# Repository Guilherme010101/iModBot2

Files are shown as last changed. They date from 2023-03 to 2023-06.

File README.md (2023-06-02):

# Project Presentation 
This iModBot project consists of a low-cost modular robot that can be programmed using block programming language and/or C/C++ language.
This project has a library to facilitate the control of the robot.

Block programming is divided into 4 levels to facilitate user learning. The levels are as follows:
 - Beginner level -> It is possible to have the robot perform a task with 1 to 2 blocks.
 - Normal level -> The user has more control over the movement of the robot, he only has the loop function.
 - Middle level -> The user can now place blocks in the Setup and Loop function.
 - Advanced level -> The user has all the functions of the library and needs to configure all aspects of the robot.
    
ROBOT

# How to transfer files from GitHub
On GitHub it's not possible to upload any file individually. It's recommended to transfer all folders and files present in this project. To do so, follow the instructions below:

Start by downloading all files in .zip format.


Open the location of the downloaded .zip file and use a program to extract the contents.


Finally you'll get a set of folders and files organized in the same way as they are in this repository.



# Project Elaboration
**1st Step of the Project**

To assemble the robot just follow the document 3-03_iModBot_Offline_Assembly_Guide ([3-03_iModBot_Offline_Assembly_Guide.pdf](https://github.com/Guilherme010101/iModBot2/blob/master/3_Documents/3-03_iModBot_Offline_Assembly_Guide.pdf)) that shows how to assemble or watch the video [iModBot@ipleiria.pt guia de montagem](https://www.youtube.com/watch?v=i4wFh0GqzkM&feature=emb_logo). This document also includes a listing of components that will be needed for its assembly. To better understand what each component of the robot does, you can read the technical manual ([3-01_iModBot_Tech_Manual.pdf](https://github.com/Guilherme010101/iModBot2/blob/master/3_Documents/3-01_iModBot_Tech_Manual.pdf)) which explains various aspects of the robot.

Material list:
 * ESP32 wroom32 devkit ; 
 <p align="center">
  
</p>

 * l293d 4 channel module ;
 <p align="center">
  
</p>   

 * 2x LM393 speed sensor ; 
 <p align="center">
  
</p> 

 * BFD-1000 5CH ;
  <p align="center">
  
</p>   

 * HC-SR04 ;
  <p align="center">
  
</p> 

 * I2C level shifter ; 
 <p align="center">
  
</p> 

 * TP4056 ; 
 <p align="center">
  
</p> 

 * li-ion rechargable battery 2500 mAh ; 
 <p align="center">
  
</p> 

 * Jumper wire male male, Jumper wire male female ; 
 <p align="center">
  
</p> 

 * 2wd smart robot kit . 
 <p align="center">
  
</p> 

**2nd Step of the Project** 
 
 Downloads:
 
- Library iModBot.rar ([4_Files/4-3_Libraries/iModBot.rar](https://github.com/Guilherme010101/iModBot2/blob/master/4_Files/4-3_Libraries/iModBot.rar)) and unzip the file. Anotação 2020-06-25 170046

- Arduino IDE software on [pagina do Arduino](https://www.arduino.cc/en/main/software), install the version that suits your equipment, for windows we recommend the option "windows installer, for windows 7 and up". 
 - Bear in mind that the project contents were developed and tested in the Arduino IDE 1.8.12 version, they should continue to be compatible with the most recent versions of this software.
       <p align="center">
  
</p> 

- ArduBlock java file ([4_Files/4-4_ArduBlock/ArduBlock_20220615.jar](https://github.com/Guilherme010101/iModBot2/blob/master/4_Files/4-4_ArduBlock/ArduBlock_20220615.jar)).

Anotação 2020-06-25 172512

**3rd Step of the Project**

Read and follow the tutorials to configure the Arduino:
 - Configure Arduino IDE for ESP32; ([3_Documents/3-04_Add_ESP32_Arduino_IDE.pdf](https://github.com/Guilherme010101/iModBot2/blob/master/3_Documents/3-04_Add_ESP32_Arduino_IDE.pdf)).

 - Configure ArduBlock in Arduino IDE; ([3_Documents/3-05_Add_ArduBlock_Arduino_IDE.pdf](https://github.com/Guilherme010101/iModBot2/blob/master/3_Documents/3-05_Add_ArduBlock_Arduino_IDE.pdf)).

 - How to install libraries in Arduino IDE. ([3_Documents/3-06_Add_Arduino_IDE_Libraries.pdf](https://github.com/Guilherme010101/iModBot2/blob/master/3_Documents/3-06_Add_Arduino_IDE_Libraries.pdf)).

# Documentation

After having the Arduino IDE and ArduBlock installed, you can take advantage of the available tutorials. These tutorials teach how to work with the robot and are divided into two categories: tutorials for ArduBlock and tutorials for Arduino IDE.

**ArduBlock documentation**

The [4 levels](https://github.com/Guilherme010101/iModBot2/tree/master/1_Tutorials/1-1_ArduBlock_Tutorials) below will facilitate and guide how to use each block and how to create a program.

- [Beginner level;](https://github.com/Guilherme010101/iModBot2/tree/master/1_Tutorials/1-1_ArduBlock_Tutorials/Tutorial_1_-_Begginer%20Level)

- [Normal level;](https://github.com/Guilherme010101/iModBot2/tree/master/1_Tutorials/1-1_ArduBlock_Tutorials/Tutorial_2_-_Normal_Level)

- [Middle level;](https://github.com/Guilherme010101/iModBot2/tree/master/1_Tutorials/1-1_ArduBlock_Tutorials/Tutorial_3_-_Intermediate_Level)

- [Advanced level.](https://github.com/Guilherme010101/iModBot2/tree/master/1_Tutorials/1-1_ArduBlock_Tutorials/Tutorial_4_-_Advanced_Level)

There is a set of activities for each level. After reading the documentation of a level, you will be able to carry out the corresponding activity in [2_Activities/2-1_ArduBlock_Activities/](https://github.com/Guilherme010101/iModBot2/tree/master/2_Activities/2-1_ArduBlock_Activities).

**Arduino IDE documentation**

After having done the ArduBock tutorials, you should have a better idea of how to program in the Arduino IDE. We've also designed some tutorials and activities to make learning easier.

- [Tutorial 1 - Movement;](https://github.com/Guilherme010101/iModBot2/tree/master/1_Tutorials/1-2_Arduino_IDE_Tutorials/Tutorial_1_-_Movement)

- [Tutorial 2 - Sensors;](https://github.com/Guilherme010101/iModBot2/tree/master/1_Tutorials/1-2_Arduino_IDE_Tutorials/Tutorial_2_-_Sensors)

- [Tutorial 3 - Follow path.](https://github.com/Guilherme010101/iModBot2/tree/master/1_Tutorials/1-2_Arduino_IDE_Tutorials/Tutorial_3_-_Follow_Path)

The activities for each tutorial are available at [2_Activities/2-2_Arduino_IDE_Activities/
](https://github.com/Guilherme010101/iModBot2/tree/master/2_Activities/2-2_Arduino_IDE_Activities).

# Edit the ArduBlock

If you are interested in creating a block, you should follow the steps in this folder [4_Files/4-4_ArduBlock/](https://github.com/Guilherme010101/iModBot2/tree/master/4_Files/4-4_ArduBlock).

# Augmented Reality

Using the Unity3d game engine, ROS2 and our robot library, create your virtual world, project it into the real world and watch the robot interact with it.
This functionality is still under development and for now it is still very limited.

# Remote controllers

With the controllers for the popular consoles PS3 and PS4, you can control the robot remotely via bluetooth. The library is easy to install and only needs one program, the Arduino IDE. Simply input desired values into the code, such as steering sensitivity, motors acceleration, maximum speed, and much more!

# Authors
 
- Abel Teixeira   - student at [Polytechnic of Leiria](https://www.ipleiria.pt/cursos/) of the TeSP course in Electronics and Telecommunications Networks, GitHub: [Ab-Tx](https://github.com/Ab-Tx)
- Samuel Lourenço - student at [Polytechnic of Leiria](https://www.ipleiria.pt/cursos/) of the TeSP course in Automation, Robotics and Industrial Maintenance, GitHub: [SamueLourenc0](https://github.com/SamueLourenc0)
- Nelson Henriques - student at [Polytechnic of Leiria](https://www.ipleiria.pt/cursos/) of the TeSP course in Automation, Robotics and Industrial Maintenance, GitHub: [NetchoExtreme](https://github.com/NetchoExtreme)
- Paulo Sousa - student at [Polytechnic of Leiria](https://www.ipleiria.pt/cursos/) of the TeSP course in Electronics and Telecommunications Networks, GitHub [DimitriOnLSD](https://github.com/DimitriOnLSD)
- Guilherme Dias - student at [Polytechnic of Leiria](https://www.ipleiria.pt/cursos/) of the TeSP course in Automation, Robotics and Industrial Maintenance, GitHub [Guilherme010101](https://github.com/Guilherme010101)

## Guided by:
- Luís Conde - [Polytechnic of Leiria](https://www.ipleiria.pt), GitHub: [Luís Conde](https://github.com/conde-ISR-UC-PT)
- Carlos Neves - [Polytechnic of Leiria](https://www.ipleiria.pt), [INESC-Coimbra](http://inescc.estg.ipleiria.pt/), GitHub: [Carlos Neves](https://github.com/carlos-neves)

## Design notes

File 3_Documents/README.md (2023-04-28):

# Documents

Inside this folder you will find documentation for the various project aspects and their respective DOCX files for editing:

- `src`
  - Word source files.

- **3-00_iModBot_Components_List.xlsx**
  - Supplies the list components used in iModBot, with some of their respective buy stores and prices.

- **3-01_iModBot_Tech_Manual.pdf**
  - Describes the components used in the project, the functions provided by the library and other aspects.

- **3-02_iModBot_Assembly_And_Software_Installation_Tutorial.pdf**
  - Teaches you how to install the necessary tools and how to assemble the robot.

- **3-03_iModBot_Offline_Assembly_Guide.pdf**
  - Provides a list of components and shows the connections that must be made between the components.

- **3-04_Add_ESP32_Arduino_IDE.pdf**
  - Explains how to connect the ESP32 development board to the Arduino IDE software.

- **3-05_Add_ArduBlock_Arduino_IDE.pdf**
  - Explains how to install ArduBlock in the Arduino IDE software.
  
- **3-06_Add_Arduino_IDE_Libraries.pdf**
  - Explains how to install libraries in the Arduino IDE software.
  
- **3-07_Edit_ArduBlock_Files.pdf**
  - It teaches how to install all the tools needed to edit the ArduBlock Workspace.

- **3-08_Create_ArduBlock_Blocks.pdf**
  - Teaches how to create a block in ArduBlock using the Eclipse IDE.

- **3-09_Add_Eclipse_IDE_Libraries.pdf**
  - Explains how to add libraries to the Eclipse IDE software.

- **3-10_Update_JDK.pdf**
  - Guide to update the Java version for using the Eclipse IDE.

- **3-11_Openblock_Error_Tutorial.pdf**
  - Troubleshooting guide for error in openblocks install.

- **3-12_Basic_Eletronics_Assembly_Guide.pdf**
  - A basic assembly guide is provided to acquaint you with the Breadboard and how it works when mounting electronic boards in this tool.

- **3-13_Remote_Bluetooth_Dualshock.pdf**
  - A tutorial is provided on how to set up the code to pair a dualshock 3 or 4 controller to control the robot remotely via Bluetooth.

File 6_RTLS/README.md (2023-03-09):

# RTLS

Folder tree:
```
6_RTLS
├── DRTLS_Manager_source_R2.0/
├── DWM1001_DWM1001-DEV_MDEK1001_Sources_and_Docs_v9/
├── Scripts/
└── esp32-dwm1001_Workspace/

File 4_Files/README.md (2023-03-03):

# Files

Folder tree:
```
4_Files
├── 4-1_PCB_Files/        // 2 PCB versions
├── 4-2_3D_Files/         // Cases for the batteries and side motor supports
├── 4-3_Libraries/        // Dualshock libraries for remote controllers and iModBot library for various other functions
└── 4-4_ArduBlock/        // ArduBlock file for Arduino IDE and ArduBlock-Workspace for editing or creating blocks
```
## Software

To be able to edit source files inside the folders, you will need the following programs:

`Eclipse IDE` This is used to edit the ArduBlock-Workspace file. In there, you can edit or create blocks, change default values or create new ones, change blocks image, etc. Tutorials for installing this program, along with JDK and maven, can be found in the 3-Documents folder.

`EAGLE` This is used to open and edit the first PCB version. 

`Proteus 8.10` This is used to open and edit the second PCB version. Keep in mind that this file can't be opened in previous versions of proteus, like 8.9.

`Fusion 360` `SolidWorks` `SketchUp Pro 2021` These can be used to open and edit the .F3D, .step and .skp files inside Battery_Case_3D folder.

`Visual Studio Code` This is used to edit the .h and .cpp files inside both libraries.

`Arduino IDE` This is used to upload the code to the ESP32.

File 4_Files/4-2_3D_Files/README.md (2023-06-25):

# 3D Battery cases

__Prototype 1__

`bat case v9.step`
Features the most recent version for single battery case for this prototype.

__Prototype 2__

`Battery_Holder.skp`
Features the most recent version for single battery case for this prototype.

`Battery_Holder_Stacked.skp`
Features an inside battery stacking with no middle layer. Simple use and faster printing but not recommended.

`Battery_Holder_Slot.skp`
Features an inside battery stacking with removable middle layer.

`Battery_Holder_Under_Robot`
Features the most recent version of the double batterry case that's under the iModBot chassis.

`Infrared_Sensor_Piece.stl`
3D printable piece to allow the sensor to work properly.

`Infrared_Sensor_Piece_Thicker_Filament.stl`
3D printable piece to allow the sensor to work properly. Should be used if the filament used to print the piece is thicker than normal.

__Others__

`motors_side_support_v3.stl`
3D printable piece for side supports in iModBot chassis.

## Information

This folder contains all cases used in iModBot for the batteries and the ifrared sensor. All outter holes dimensions are specifically designed for the iModBot chassis alone. 

Sterolithography files (STL) can be opened directly with CURA software for 3D printing. 

SketchUp (SKP), Fusion 360 (F3D), Standard for the Exchange of Product Data (STEP) and Autodesk Inventor Part files are the given open-source files. SkethUp files were saved with 2021 version.

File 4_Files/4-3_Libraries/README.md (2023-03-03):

# Dualshock and iModBot Libraries

These libraries were written in C/C++ programming language. You will find instructions on how to install these and upload them to the ESP32 inside the  [3-Documents](https://github.com/Guilherme010101/iModBot2/tree/master/3_Documents) folder. Inside you can also find information regarding the robots' various functions.

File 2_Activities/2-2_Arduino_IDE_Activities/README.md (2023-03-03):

# Atividades para Arduino IDE

As presentes atividades podem ser realizadas com recurso ao software Arduino IDE utilizando a linguagem de programação C/C++.

Ps tutoriais associados estão presentes em [/1_Tutoriais/1-2_Tutoriais_para_Arduino_IDE/](https://github.com/Guilherme010101/iModBot2/tree/master/1_Tutorials/1-2_Arduino_IDE_Tutorials).

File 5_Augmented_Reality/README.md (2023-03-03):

# Augmented Reality

Using the Unity3d game engine, ROS2 and our robot library, create your virtual world, project it into the real world and watch the robot interact with it.

This functionality is still under development and for now it is still very limited.

## Requirements

 - Ubuntu 20.04 (Native ou Virtual)
 - Consult the document [Tutorial_SetUp_VM](https://github.com/Guilherme010101/iModBot2/blob/master/5_Augmented_Reality/Tutorial_SetUp_VM.pdf) to install it on a Virtual Machine (native installation is recommended).
 
 - Docker  
 - Consult the document [Tutorial_docker](https://github.com/Guilherme010101/iModBot2/blob/master/5_Augmented_Reality/Tutorial_docker.pdf) to install it and understand how it works.

## Utilization

1. Open a terminal in the folder [iModBot-Docker](https://github.com/Guilherme010101/iModBot2/tree/master/5_Augmented_Reality/iModBot-Docker).
   
2. Create the Docker image (this step takes some time).
    ```bash
    $ ./build-docker-image.bash
    ```
3. Starts the created image.
    ```bash
    $ ./run-docker-container
    ```
4.  Open the `VScode`.
    ```bash
    $ code
    ```
	  -  Install the PlatformIO extension and open the folder [VScode_Workspace\ESP32-ROS2_iModBot](https://github.com/Guilherme010101/iModBot2/tree/master/5_Augmented_Reality/iModBot-Docker/VScode_Workspace/ESP32-ROS2_iModBot), put the id and password of your Wifi network and the IP of the container.
	  - Uploads the program to the ESP32.
	  - Save changes and close VScode.
    
5. Start the `Unity Hub` and install the latest editor and open the project found in the folder [iModBot-Docker\Unity_Workspace](https://github.com/Guilherme010101/iModBot2/tree/master/5_Augmented_Reality/iModBot-Docker/Unity_Workspace/iModBot-UnityRos2).
    ```bash
    $ cd unity && ./UnityHub.AppImage
    ```
6.  Start the ROS2 Node.
 - In the terminal of the native machine that is in the folder iModBot-Docker opens a new terminal in the container.
    ```bash
    $ ./new_bash_in_container
    ```
 - In the new terminal:
    ```bash
    $ cd work/ROS2_Workspace && . install/setup.bash && ros2 run stop_oncollision oncollision
    ```
7. Starts the remote control (it can be accessed in any browser as long as it is on the local network, through the IP that appears in the window).
- Open 2 new terminals in the container, as described earlier.
- On the 1st:
    ```bash
    $ cd ros2-web-bridge && export DEBUG=ros2-web-bridge:* && node bin/rosbridge.js
    ```
- On the 2nd:
    ```bash
    $ cd ros2-web-bridge/demo && http-server -c-1
    ```
 
8. Start the MicroXRCEAgent (responsible for establishing communication between ROS2 and ESP32).
- Opens a new terminal in the container.
- Starts the program.
    ```bash
    $ MicroXRCEAgent udp4 -p 2018
    ```
Everything is ready to start your journey with augmented reality.
Whenever you want to reopen the container, run the script [start-docker-container](https://github.com/Guilherme010101/iModBot2/blob/master/5_Augmented_Reality/iModBot-Docker/start-docker-container.bash).

Demo video: [https://youtu.be/DlAx3p5d99E](https://youtu.be/DlAx3p5d99E)

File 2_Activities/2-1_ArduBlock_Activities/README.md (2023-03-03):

# Atividades para ArduBlock

Os presentes tutoriais deverão facilitar a compreensão da linguagem de programaçãopor blocos bem como o seu uso no presente projeto.

Pode encontrar os tutoriais associados em [/1_Tutoriais/1-1_Tuturiais_para_ArduBlock/](https://github.com/Guilherme010101/iModBot2/tree/master/1_Tutorials/1-1_ArduBlock_Tutorials).

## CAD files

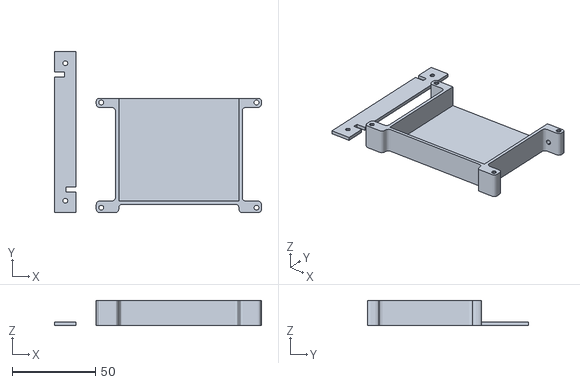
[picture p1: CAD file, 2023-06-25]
4_Files/4-2_3D_Files/Battery_Holden_Under_Robot.stl
124.0 x 96.7 x 15.0

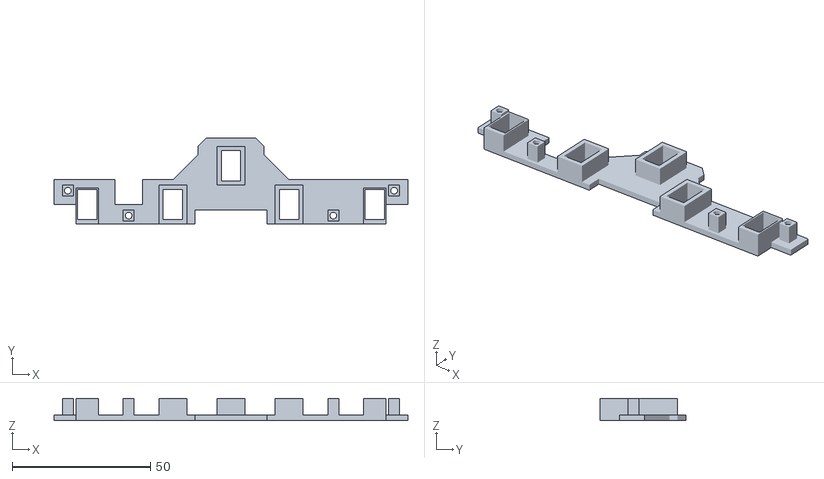
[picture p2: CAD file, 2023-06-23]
4_Files/4-2_3D_Files/Infrared_Sensor_Piece_Thicker_Filament.stl
128.0 x 31.0 x 8.00

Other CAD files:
4_Files/4-2_3D_Files/Infrared_Sensor_Piece.stl
4_Files/4-2_3D_Files/Batterry_Holder_Under_Robot.ipt
4_Files/4-2_3D_Files/Infrared_Sensor_Piece.ipt
4_Files/4-2_3D_Files/Infrared_Sensor_Piece_Thicker_Filament.ipt

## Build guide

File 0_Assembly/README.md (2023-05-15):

# Assembly

PDF files on the main folder and DOCX files on the src folder with instructions on how to assemble the robot and install the necessary tools, and how to upload sketches to ESP32 OTA (Over The Air), with an arduino file on the main folder.

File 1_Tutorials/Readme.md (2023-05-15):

# Tutorials

Tutorials for ArduBlock contain educational content for block programming.

The tutorials for Arduino IDE contain educational content for C/C++ programming.

Activities are provided for each tutorial, they can be found in [2_Activities](https://github.com/Guilherme010101/iModBot2/tree/master/2_Activities).

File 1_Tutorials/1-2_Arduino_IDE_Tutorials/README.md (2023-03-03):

# Tutoriais para Arduino IDE

Os presentes tutoriais deverão facilitar a compreensão da linguagem de programação C/C++ bem como o seu uso no presente projeto.

Pode encontrar as atividades associadas em [/2_Atividades/2-2_Atividades_para_Arduino_IDE/](https://github.com/Guilherme010101/iModBot2/tree/master/2_Activities/2-2_Arduino_IDE_Activities).

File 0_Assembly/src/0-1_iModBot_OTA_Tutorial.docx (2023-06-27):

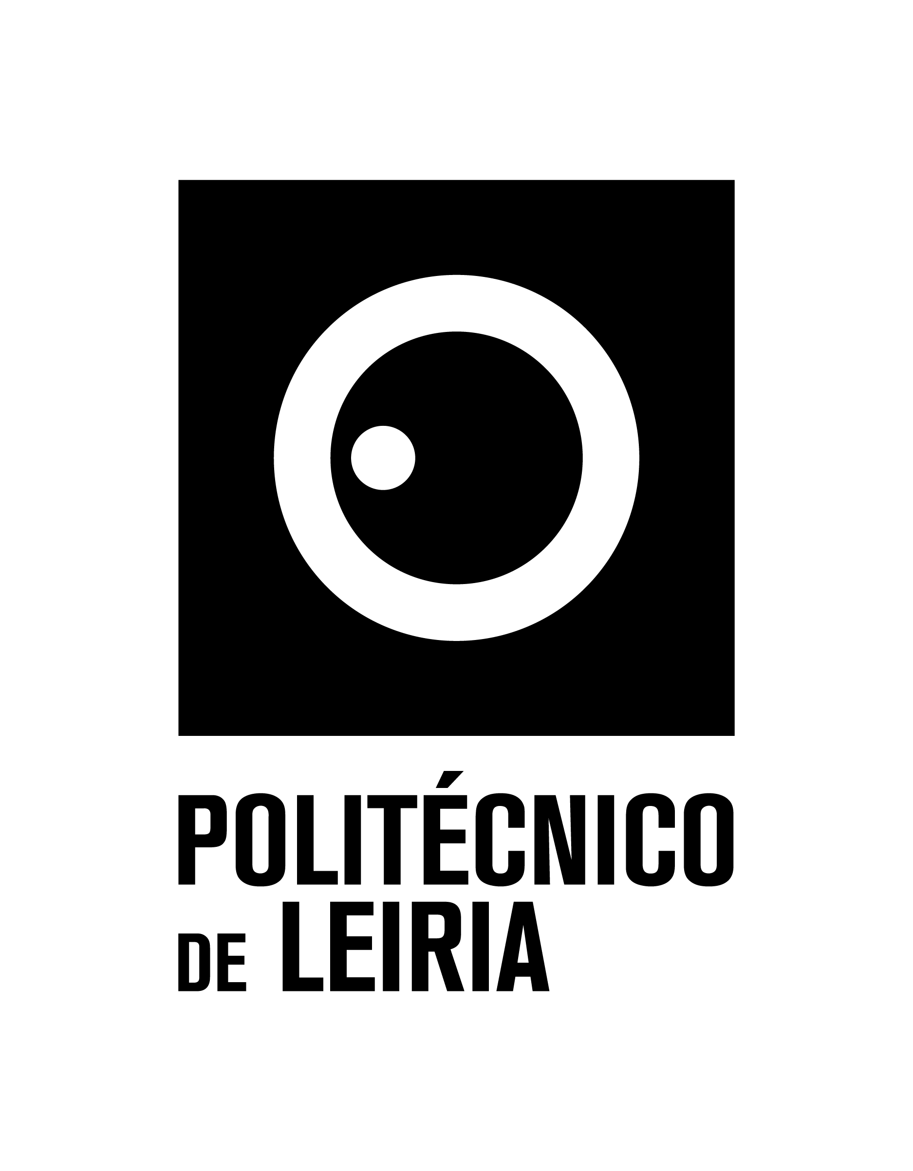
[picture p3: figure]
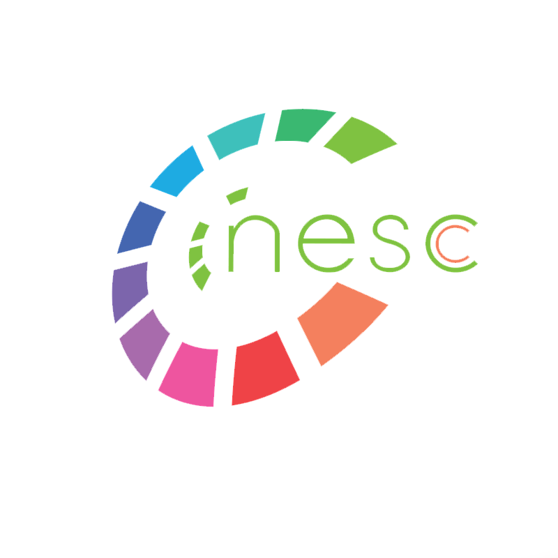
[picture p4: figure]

| Guia de montagem iModBot@ipleiria.pt

# Tutorial de como carregar programas para o ESP32 via WiFi

O robô iModBot é um veículo elétrico de pequenas proporções controlado pelo microcontrolador ESP32. Este microcontrolador pode ser programado usando a linguagem C/C++ e o software gratuito Arduino IDE.

Este tutorial vai focar-se na funcionalidade OTA (Over the Air), que permite carregar programas para o ESP32 usando uma conexão WiFi em vez de se utilizar um cabo entre o computador e o microcontrolador. Este tipo de funcionalidade é essencial para este projeto porque a estrutura do iModBot não permite uma conexão física entre o computador e o ESP32, visto que a sua entrada USB está bloqueada pela caixa das baterias, e assim não é necessário estar a tirar e pôr o ESP32 na placa sempre que seja preciso inserir um novo programa.

1º Passo: Conecte o ESP32 ao seu computador através de um cabo micro-usb.

2º Passo: Vá a “Ferramentas” e selecione o modelo da placa ESP32 e a respetiva porta COM.

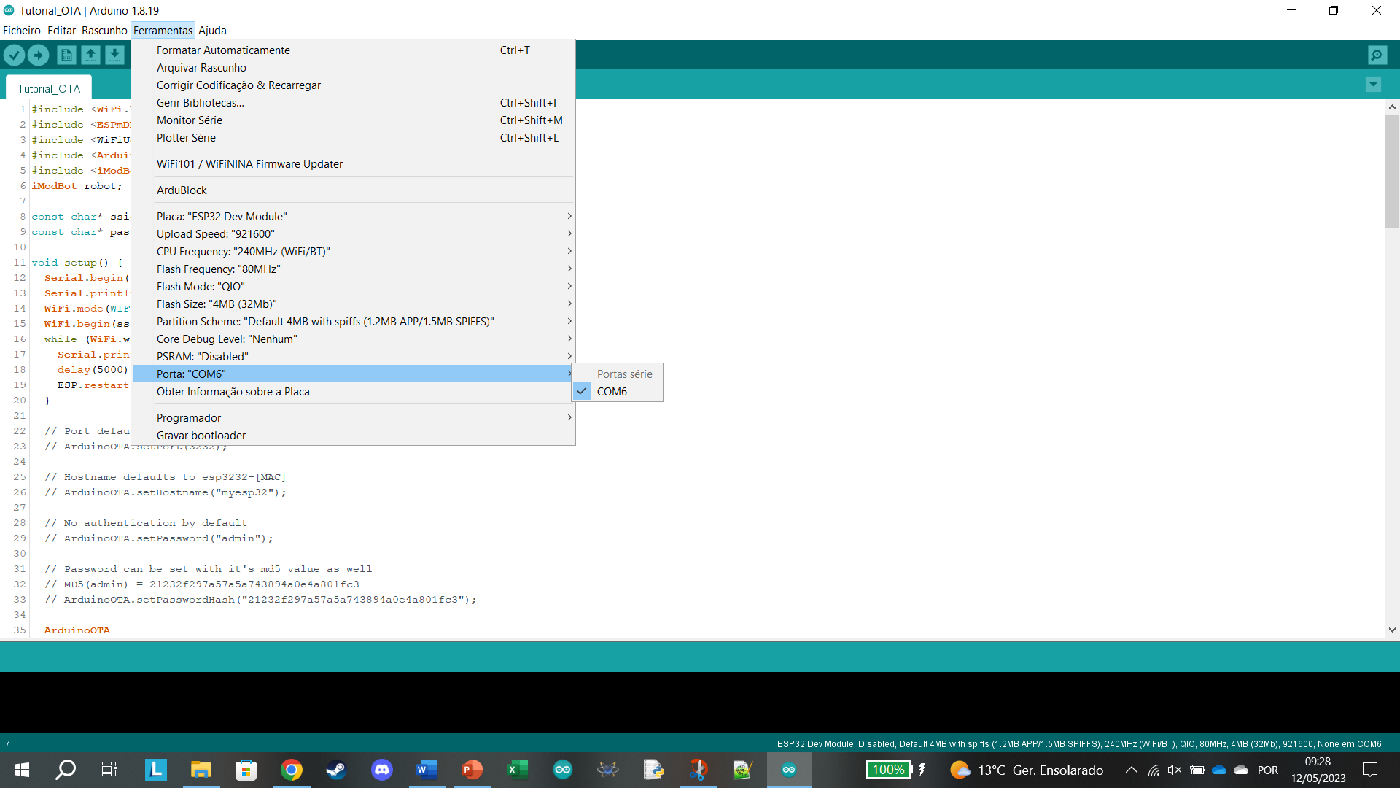
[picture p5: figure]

3º Passo: Copie o seguinte código para o Arduino IDE e nele mude o “ssid” e a “password” pelo nome da rede e a sua palavra-passe, respetivamente:

#include <WiFi.h>

#include <ESPmDNS.h>

#include <WiFiUdp.h>

#include <ArduinoOTA.h>

// Replace with your network credentials

const char* ssid = "YOUR_SSID";

const char* password = "YOUR_PASSWORD";

void setup() {

Serial.begin(115200);

Serial.println("Booting");

WiFi.mode(WIFI_STA);

WiFi.begin(ssid, password);

while (WiFi.waitForConnectResult() != WL_CONNECTED) {

Serial.println("Connection Failed! Rebooting...");

delay(5000);

ESP.restart();

}

// Port defaults to 3232

// ArduinoOTA.setPort(3232);

// Hostname defaults to esp3232-[MAC]

// ArduinoOTA.setHostname("myesp32");

// No authentication by default

// ArduinoOTA.setPassword("admin");

// Password can be set with it's md5 value as well

// MD5(admin) = 21232f297a57a5a743894a0e4a801fc3

// ArduinoOTA.setPasswordHash("21232f297a57a5a743894a0e4a801fc3");

ArduinoOTA

.onStart([]() {

String type;

if (ArduinoOTA.getCommand() == U_FLASH)

type = "sketch";

else // U_SPIFFS

type = "filesystem";

// NOTE: if updating SPIFFS this would be the place to unmount SPIFFS using SPIFFS.end()

Serial.println("Start updating " + type);

})

.onEnd([]() {

Serial.println("\nEnd");

})

.onProgress([](unsigned int progress, unsigned int total) {

Serial.printf("Progress: %u%%\r", (progress / (total / 100)));

})

.onError([](ota_error_t error) {

Serial.printf("Error[%u]: ", error);

if (error == OTA_AUTH_ERROR) Serial.println("Auth Failed");

else if (error == OTA_BEGIN_ERROR) Serial.println("Begin Failed");

else if (error == OTA_CONNECT_ERROR) Serial.println("Connect Failed");

else if (error == OTA_RECEIVE_ERROR) Serial.println("Receive Failed");

else if (error == OTA_END_ERROR) Serial.println("End Failed");

});

ArduinoOTA.begin();

Serial.println("Ready");

Serial.print("IP address: ");

Serial.println(WiFi.localIP());

}

void loop() {

ArduinoOTA.handle();

}

4º Passo: Pressione em “Envio”, que é o botão com uma seta a apontar para a direira no canto superior esquerdo, e ao mesmo tempo que está a enviar o programa pressione o botão “Boot” do ESP32 para que ele permitir carregar o programa.

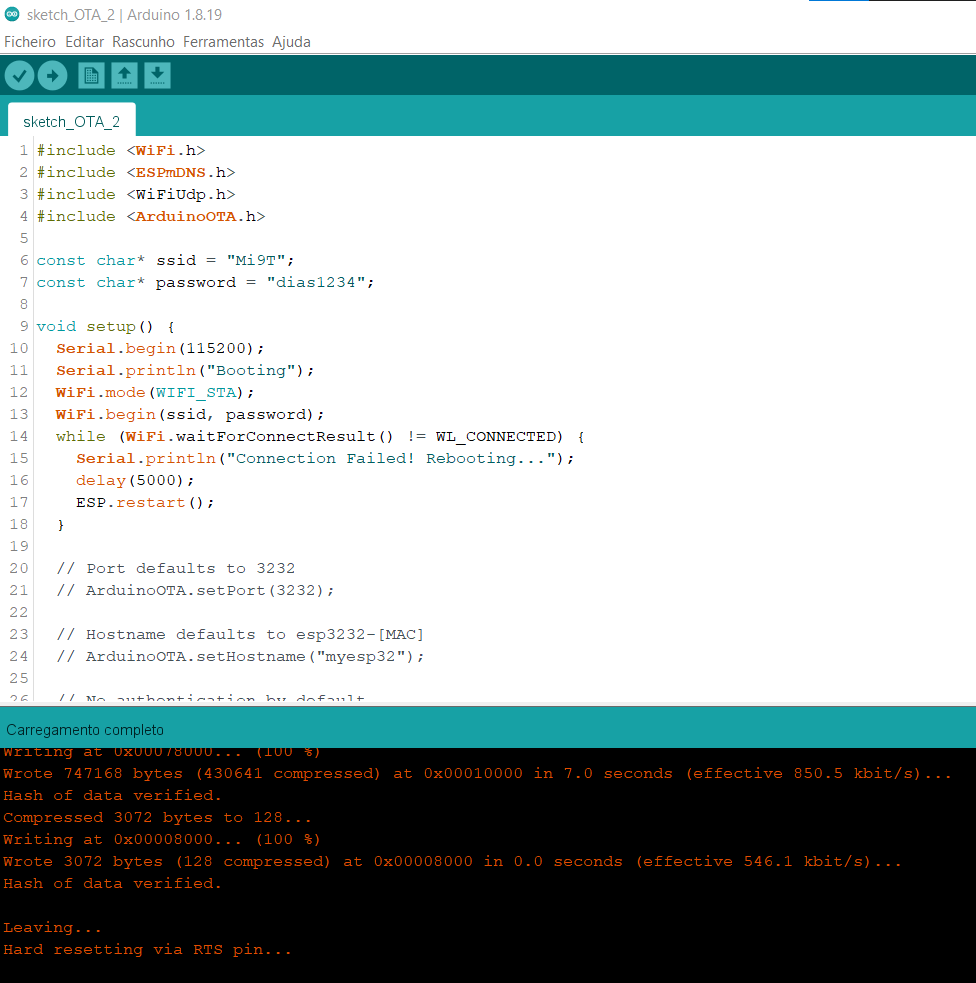
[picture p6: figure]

5º Passo: Abra o “Monitor série” do Arduino IDE, que é o botão com uma lupa no canto superior direito, pressione o botão “EN” do ESP32 para fazer reset e se inseriu as credenciais certa da rede deverá aparecer o endereço IP do ESP.

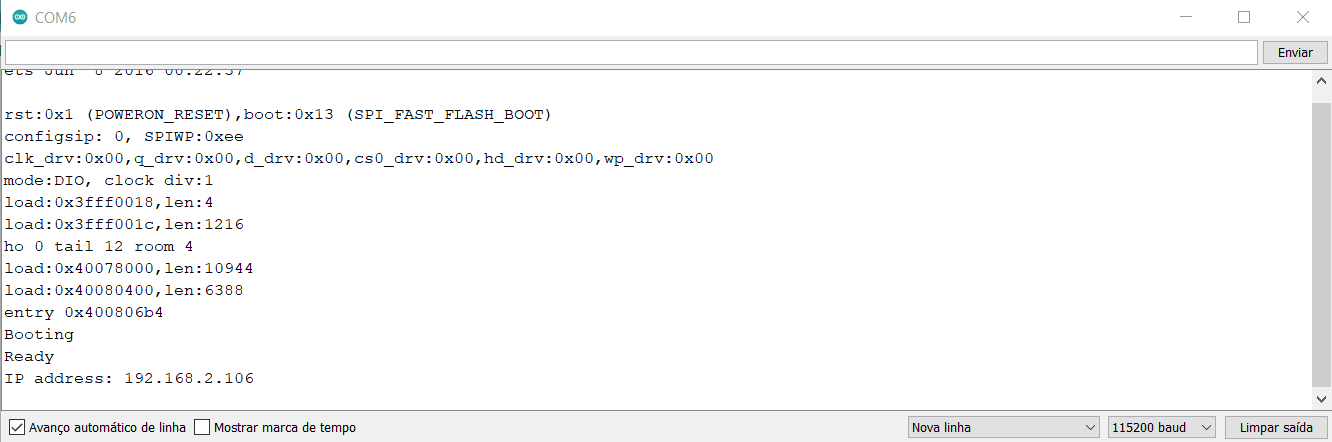
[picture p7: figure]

6º Passo: Agora que o ESP32 está preparado para receber programas OTA, desconecte o microcontrolador do computador, insira-o na placa do iModBot e ligue o robô.

7º Passo: Abra o Arduino IDE, selecione “Ferramentas” e selecione a Porta de rede do ESP32, que deverá ter um aspeto semelhante ao da imagem abaixo:

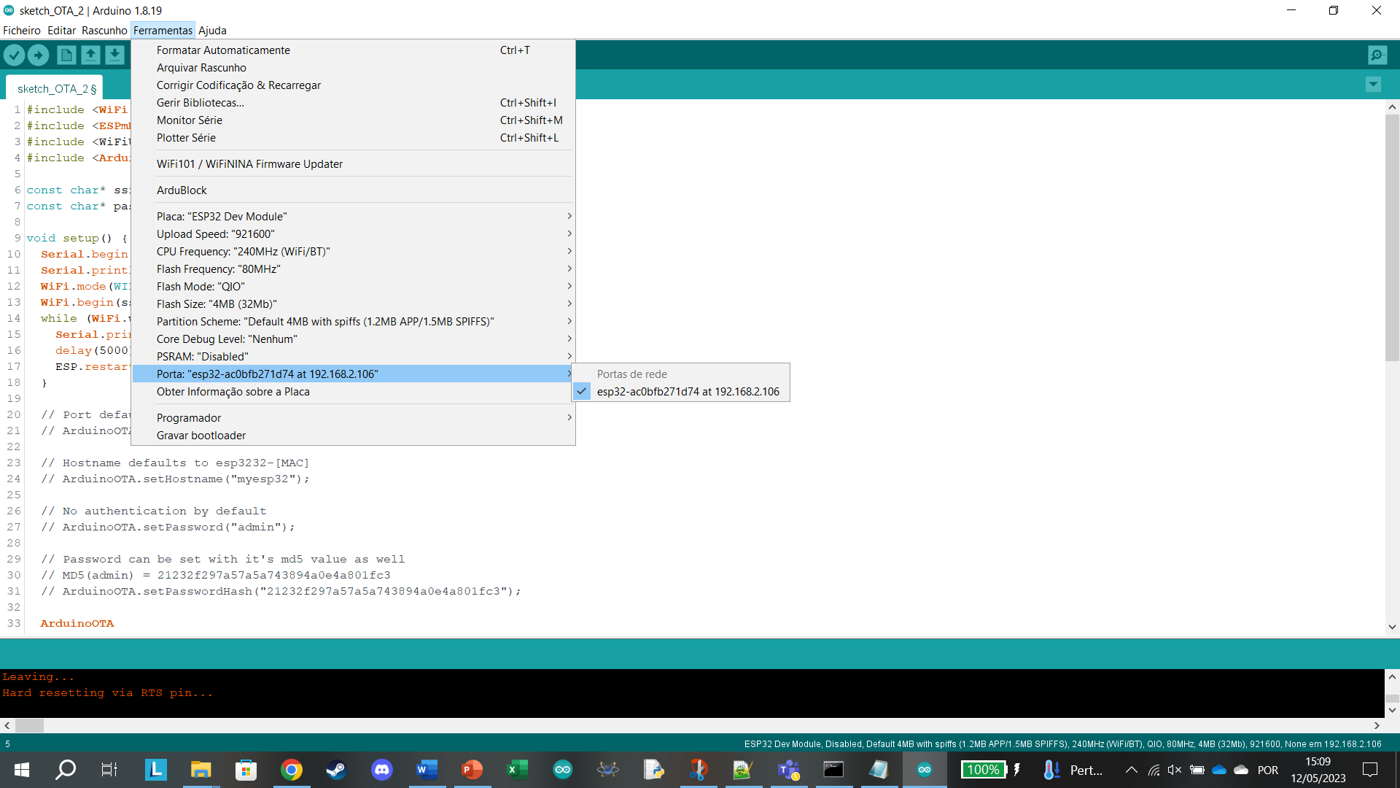
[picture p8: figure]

8º Passo: Com o ESP32 conectado via WiFi basta inserir o código. Para que o código seja compatível com o OTA é necessário inserir o código em si no código básico do OTA. Em baixo está o código do tutorial de controlo de movimentos simples do iModBot sem e com as propriedades do OTA, respetivamente.

### Exemplo controlo de movimentos simples

#include <iModBot.h>

iModBot robot;

void setup()

{

robot.begin();

}

void loop()

{

// Velocidade

// Pode variar de 1 a 255

byte speed = 255;

// Para seguir em frente

robot.forward(speed);

delay(500);

// Para recuar

robot.reverse(speed);

delay(500);

// Rodar para a direita

robot.rotateRight(speed);

delay(500);

// Rodar para a esquerda

robot.rotateLeft(speed);

delay(500);

// Parar os motores

robot.stopMotors();

delay(1000);

}

### Exemplo controlo de movimentos simples com OTA

#include <WiFi.h>

#include <ESPmDNS.h>

#include <WiFiUdp.h>

#include <ArduinoOTA.h>

#include <iModBot.h>

iModBot robot;

// Replace with your network credentials

const char* ssid = "YOUR_SSID";

const char* password = "YOUR_PASSWORD";

void setup() {

Serial.begin(115200);

Serial.println("Booting");

WiFi.mode(WIFI_STA);

WiFi.begin(ssid, password);

while (WiFi.waitForConnectResult() != WL_CONNECTED) {

Serial.println("Connection Failed! Rebooting...");

delay(5000);

ESP.restart();

}

// Port defaults to 3232

// ArduinoOTA.setPort(3232);

// Hostname defaults to esp3232-[MAC]

// ArduinoOTA.setHostname("myesp32");

// No authentication by default

// ArduinoOTA.setPassword("admin");

// Password can be set with it's md5 value as well

// MD5(admin) = 21232f297a57a5a743894a0e4a801fc3

// ArduinoOTA.setPasswordHash("21232f297a57a5a743894a0e4a801fc3");

ArduinoOTA

.onStart([]() {

String type;

if (ArduinoOTA.getCommand() == U_FLASH)

type = "sketch";

else // U_SPIFFS

type = "filesystem";

// NOTE: if updating SPIFFS this would be the place to unmount SPIFFS using SPIFFS.end()

Serial.println("Start updating " + type);

})

.onEnd([]() {

Serial.println("\nEnd");

})

.onProgress([](unsigned int progress, unsigned int total) {

Serial.printf("Progress: %u%%\r", (progress / (total / 100)));

})

.onError([](ota_error_t error) {

Serial.printf("Error[%u]: ", error);

if (error == OTA_AUTH_ERROR) Serial.println("Auth Failed");

else if (error == OTA_BEGIN_ERROR) Serial.println("Begin Failed");

else if (error == OTA_CONNECT_ERROR) Serial.println("Connect Failed");

else if (error == OTA_RECEIVE_ERROR) Serial.println("Receive Failed");

else if (error == OTA_END_ERROR) Serial.println("End Failed");

});

ArduinoOTA.begin();

Serial.println("Ready");

Serial.print("IP address: ");

Serial.println(WiFi.localIP());

robot.begin();

}

void loop() {

ArduinoOTA.handle();

// Velocidade

// Pode variar de 1 a 255

byte speed = 255;

// Para seguir em frente

robot.forward(speed);

delay(500);

// Para recuar

robot.reverse(speed);

delay(500);

// Rodar para a direita

robot.rotateRight(speed);

delay(500);

// Rodar para a esquerda

robot.rotateLeft(speed);

delay(500);

// Parar os motores

robot.stopMotors();

delay(1000);

### }

Tutorial – Movimento iModBot@ipleiria.pt Página 30 de 30

Politécnico de Leiria 2022/2023

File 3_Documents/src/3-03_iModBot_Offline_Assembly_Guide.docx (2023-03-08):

GUIA DE MONTAGEM

Passo 1:

Este documento irá servir de guia para a montagem do robô iModBot@ipleiria.pt.

Como instalar o Arduino IDE:
https://support.arduino.cc/hc/en-us/articles/360019833020-Download-and-install-Arduino-IDE

Foi criada uma biblioteca para facilitar a programação do robô, a mesma está disponível em:
---
Passo 2:

Video demonstrativo de como instalar a biblioteca:

https://youtu.be/pUydwEE_rCo

Foi criada uma versão personalizada do Ardublocks que possui novos blocos que permitem o controlo do robô.
A mesma está disponível em:
---

Passo 3:

Video demonstrativo de como instalar o Ardublocks:

https://youtu.be/oaflX_1ZpHQ

Estabeleças as ligações como demonstrado nas imagens.

Também está disponível um vídeo que demonstra a montagem dos vários componentes:

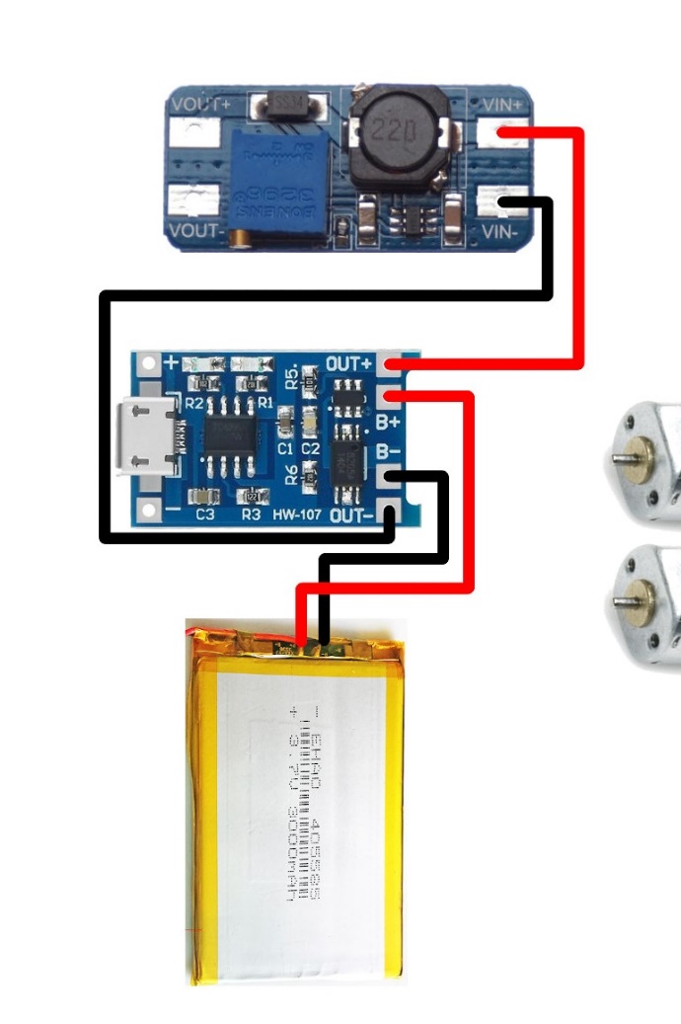
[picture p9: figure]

Figura 1 - Passo 1

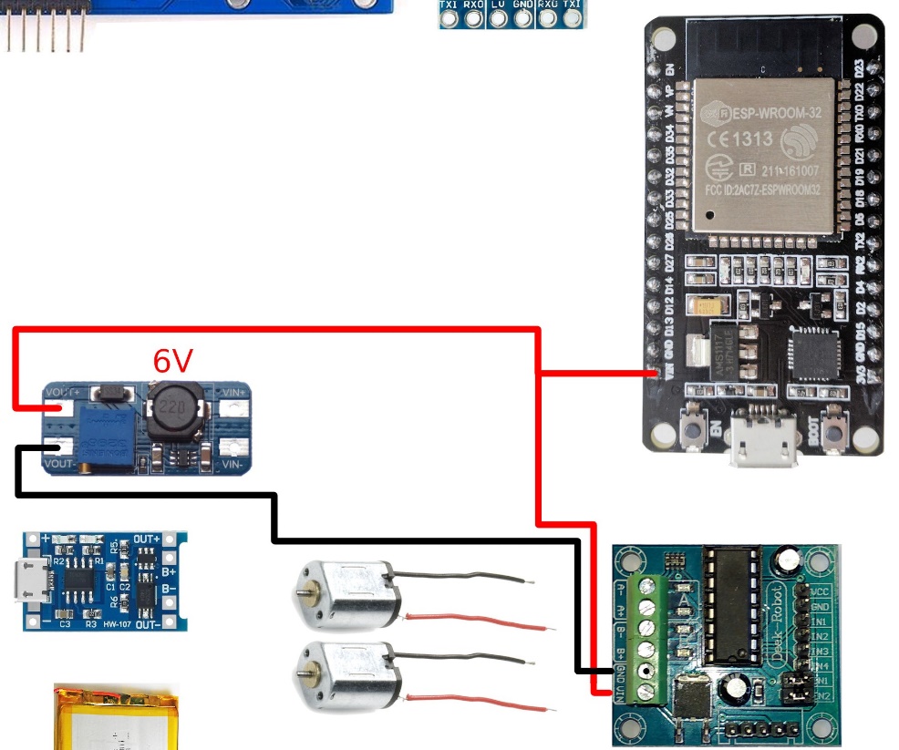
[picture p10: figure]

Figura 2 - Passo 2

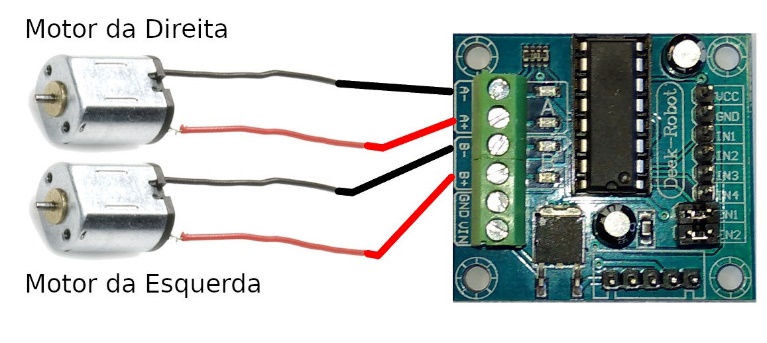
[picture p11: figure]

Figura 3 - Passo 3

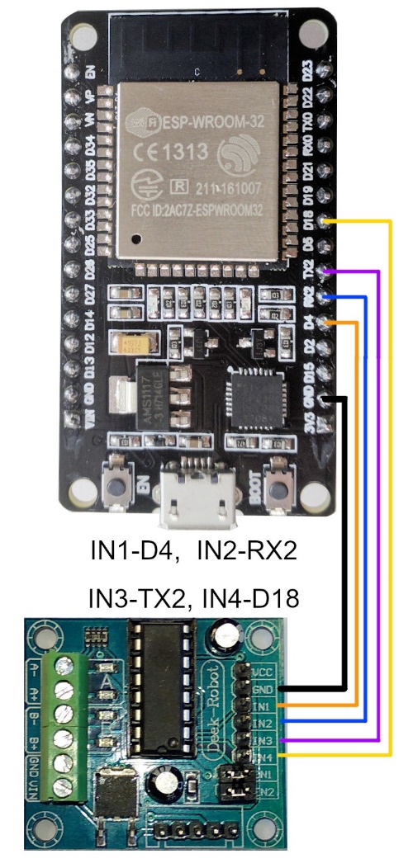
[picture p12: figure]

Figura 4 - Passo 4

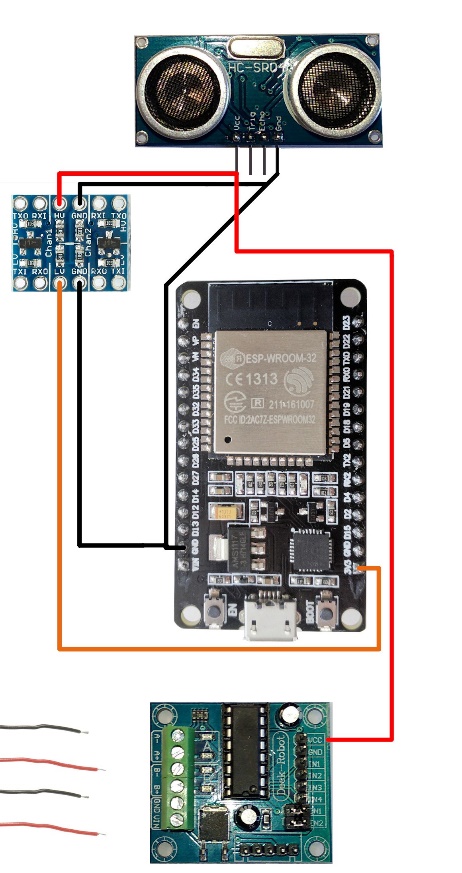
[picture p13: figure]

Figura 5 - Passo 5

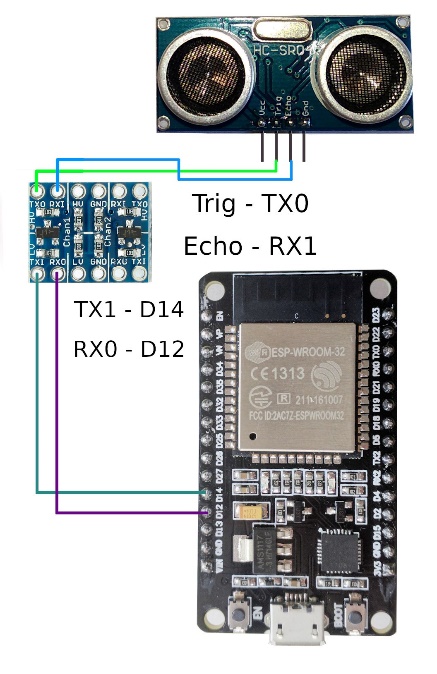
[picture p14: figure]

Figura 6 - Passo 6

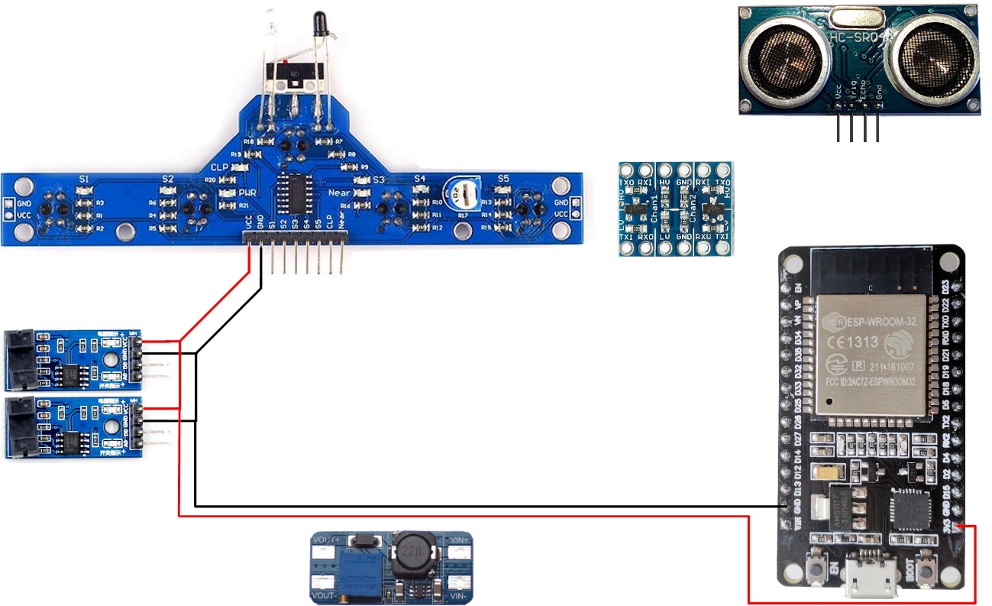
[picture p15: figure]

Figura 7 - Passo 7

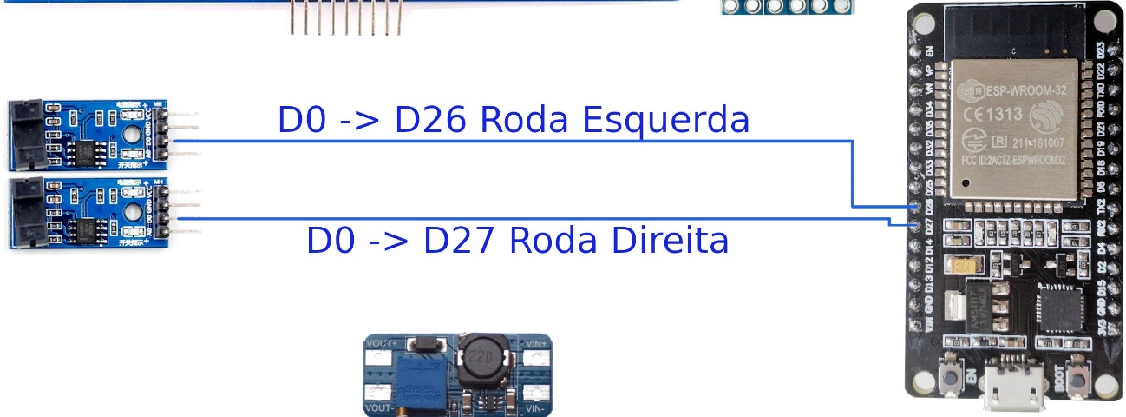
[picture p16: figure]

Figura 8 - Passo 8

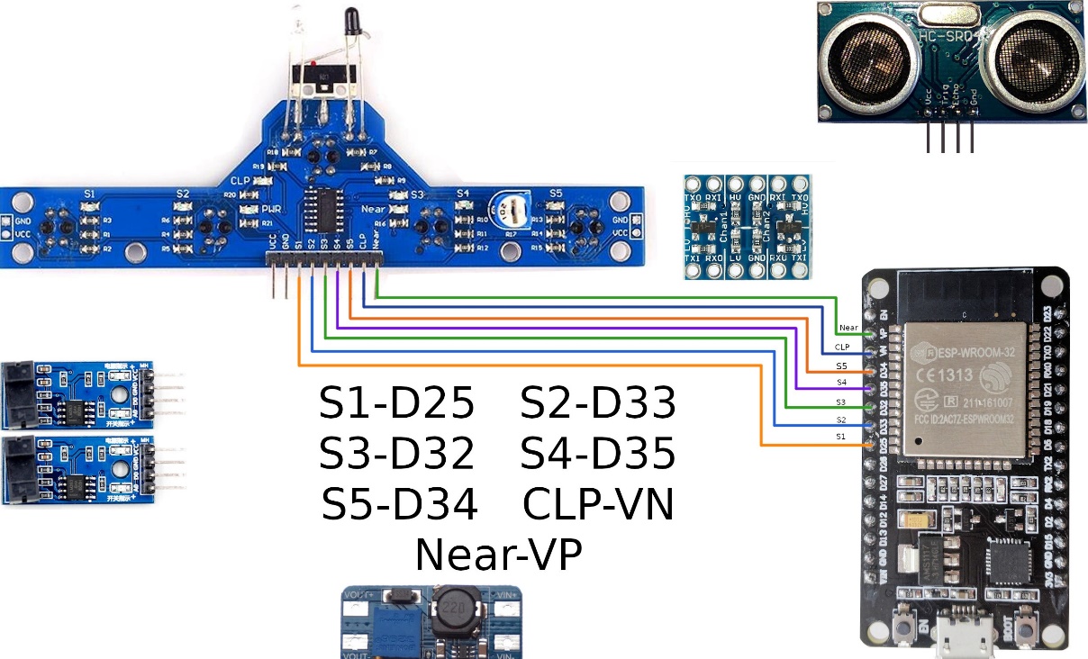
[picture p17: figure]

Figura 9 - Passo 9

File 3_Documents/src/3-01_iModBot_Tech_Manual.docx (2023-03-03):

# Manual Técnico iModRob@ipleiria.pt

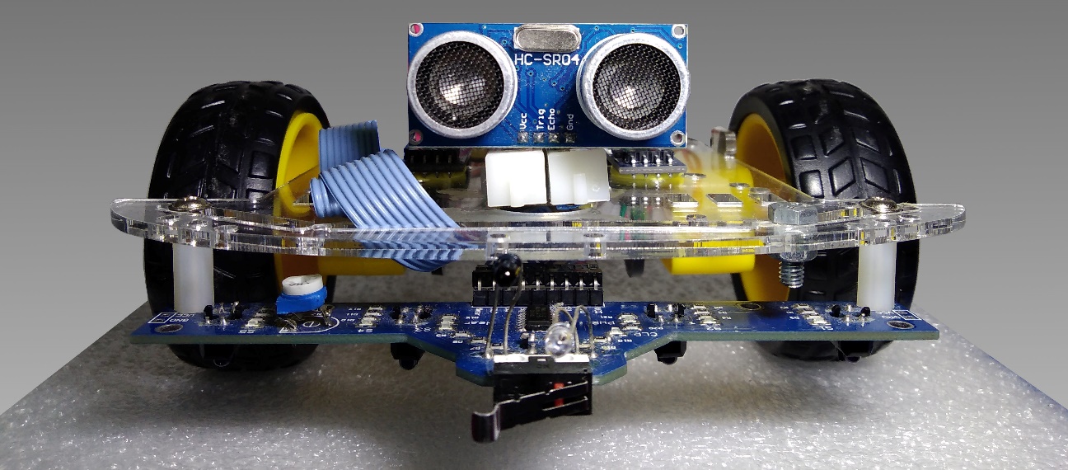
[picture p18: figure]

# Índice

# Introdução

O projeto iModBot@ipleiria.pt consiste num robô seguidor de linha, modular, de baixo custo.

É fornecida uma biblioteca escrita em C/C++ para facilitar o uso do mesmo.

Este robô pode ser programado através da aplicação Arduino IDE em linguagem C/C++ e também através de linguagem de programação por blocos utilizando o software ArduBlocks.

Neste documento serão descritos os componentes, as ligações dos mesmo e o uso da biblioteca.

# Descrição dos componentes

- DOIT ESP32 DevKit V1

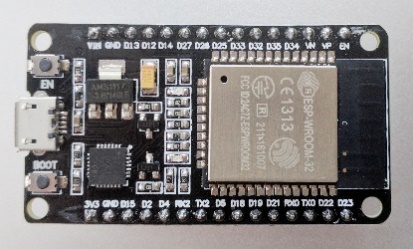
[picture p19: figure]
DOIT ESP32 DEVKIT V1 Board · Issue #544 · espressif ...

A placa de desenvolvimento DOIT ESP32 DevKit V1 irá controlar o robô e todos os seus periféricos. Esta placa é baseada no microcontrolador ESP32 desenvolvido pela Espressif Systems. Este microcontrolador possui uma velocidade de 80 até 240 MHz (dependendo da versão e/ou configuração), 4MB de memória flash e 520KB de SRAM.

Tensão de entrada do módulo: 5 a 12V.

Tensão de operação: 3.3V.

Wi-Fi: IEEE 802.11 b/g/n/e/i.

Bluetooth BLE.

- Módulo de controlo dos motores, L293D

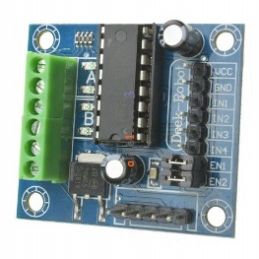
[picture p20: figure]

Este módulo servirá para controlar os motores.
No bloco terminal (VIN) pode ser conectada uma tensão de 7 até 35 V que irá alimentar o regulador 78M05 que por sua vez irá fornecer uma tensão de 5 V.
São necessários quatro pinos para controlar os dois motores, pode ser usada modulação de largura de pulsos (PWM) para controlar a velocidade dos motores.

Tensão de entrada no pino VIN: 7 a 35 V.

Corrente fornecida pelo 78M05: 500mA.

Nota: Forneça alimentação ao módulo apenas através do pino VIN. O pino VCC é uma saída e está conectado à saída do regulador 78M05 (presente na placa do módulo) que fornece 5 V.

- Placa de sensores IR 74HC14

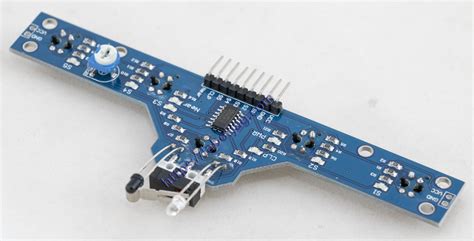
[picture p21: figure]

A placa de sensores infravermelhos possui seis emissores e seis recetores infravermelhos para possibilitar a deteção de linhas. Os recetores infravermelhos estão ligados a um inversor com histerese 74HC14 que irá evitar ruído nas ligações do mesmo à placa de desenvolvimento DOIT ESP32 DevKit V1. O sensor “Near” pode obter falsos-positivos devido à luz natural/ambiente.

A tensão de entrada (VCC) é de 2 a 6 V.

- Encoder Óticos

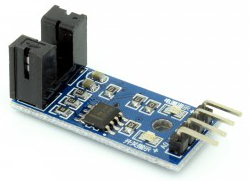
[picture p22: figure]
Motor Speed Encoder Sensor | Open ImpulseOpen Impulse

Os sensores óticos servem para obter um feedback da rotação das rodas podendo deste modo obter a distância percorrida e saber se uma está a rodar mais rapidamente que a outra.

Tensão de operação: 3.3 a 5 V.

- HC-SR04

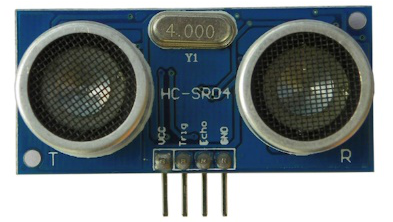
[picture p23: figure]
นาย arduino: ใช้ Arduino ติดต่อกับ Ping Ultrasonic Sensor ...

O sensor ultrassónico HC-SR04 permite detetar obstáculos com antecedência.

Tensão de operação: 5 V.

Consumo de corrente típico: 15mA.

Frequência de funcionamento: 40 MHz.

Alcance: desde 2cm até 4m.

Angulo de medição: 15º.

Tempo do sinal de gatilho: 10us nível TTL.

- Módulo de carga TP4056

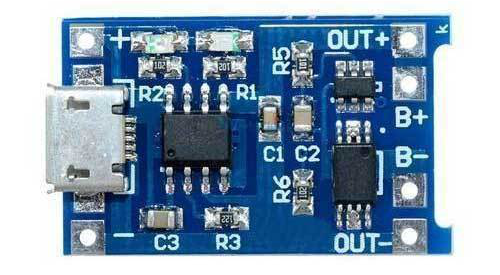
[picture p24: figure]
Lithium Ion Battery Charging Module TP4056, Voltage: 220 ...

O módulo baseado no circuito integrado TP4056 permite carregar baterias de iões lítio.
Possui um LED vermelho que indica que a bateria está a ser carregada e um LED azul que indica que o carregamento foi concluído.

Tensão de entrada: 4,5 a 8V.

Carrega a bateria até 4,2V ao máximo de 1A.

A potência de saída é a potência da bateria, tendo um máximo de 3 amperes limitado por um MOSFET.

- Módulo elevador de tensão MT3608

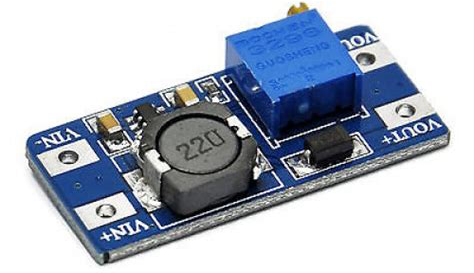
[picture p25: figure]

O módulo baseado no circuito integrado MT3608 efetua uma elevação de tensão ajustável.

A eficiência máxima é cerca de 93%, quanto maior for a diferença entre tensão de entrada/saída menor será a eficiência.

Tensão de entrada: 2 a 24 V.

Tensão de saída ajustável: 5 a 28V.

Corrente máxima fornecida (pico): 2A.

- Bateria de lítio de iões

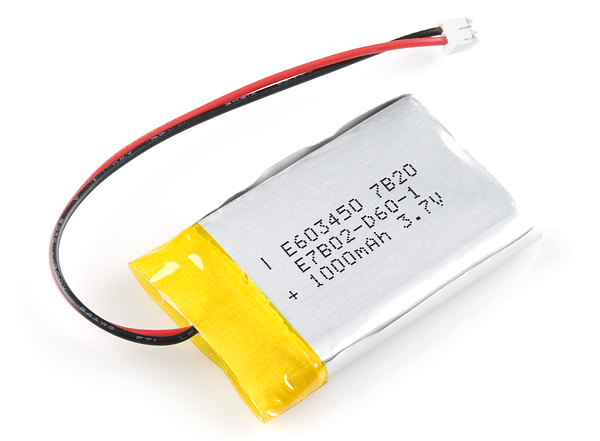
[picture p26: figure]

Para o projeto foi usada uma bateria de lítio de iões.

Este tipo de baterias são normalmente acessíveis e possuem bastante autonomia.

# Recursos do ESP32 usados pela biblioteca

A biblioteca iModBot usa os seguintes recursos do ESP32:

- 28 748 bytes de memória Flash (2,2%);
- Timer nº 0;
- Canais PWM nº 0, 1, 2 e 3;
- Canal nº 0 do periférico “Pulse Counter” nº 0;
- Canal nº 0 do periférico “Pulse Counter” nº 1.

# Descrição das funções da biblioteca

Nota: A contagem de pulsos dos enconder óticos é efetuada por hardware usando um módulo denominado de “pulse counter”. A configuração deste módulo encontra-se dentro das bibliotecas “E32_PC0” e “E32_PC1”. Quando a biblioteca “RobotOnLine” é usada estas outras duas bibliotecas serão incluídas automaticamente. Não é necessário incluir as bibliotecas “E32_PC0” e “E32_PC1” no programa que use a biblioteca “RobotOnLine”, o ambiente Arduino IDE poderá incluir as mesmas por defeito, estas inclusões pode ser apagadas.

- Void editWheelPin(uint8_t ,uint8_t )

Permite alterar os pinos onde são ligados os sensores óticos.

Se esta função for usada, a mesma deve ser chamada antes da função “begin()”.

Por defeito os pinos usados para os sensores óticos são o 26 e 27.

Os parâmetros são encoder da esquerda, encoder da direita respetivamente.

- Void editMotorPin(uint8_t ,uint8_t , uint8_t ,uint8_t ,)

Permite alterar onde são ligadas as conceções para controlar os motores.

Por defeito os pinos usados são o 2, 4, 16 e 17.

Os parâmetros são IN1, IN2, IN3, IN4 respetivamente.

- Void editUltrasonicPin(uint8_t ,uint8_t )

Esta função permite alterar os pinos que conectam ao sensor ultrassónico HC-SR04.

Por defeito os pinos usados são o 14 e o 12.

Os parâmetros são trig, echo respetivamente.

- Void editSensorPin(uint8_t ,uint8_t , uint8_t ,uint8_t , uint8_t ,uint8_t , uint8_t)

Permite alterar os pinos onde são estabelecidas as ligações à placa frontal que possui vários sensores de infravermelho.

Caso use a função de condução autónoma (seguir um trajeto de forma autónoma) da biblioteca, deve chamar esta função antes da função “beginAutoDrive();”

Por defeito os pinos usados são 25, 33, 32, 35, 34, 39, 36.

Os parâmetros são S1, S2, S3, S4, S5, CLP, Near respetivamente.

- Void setStopDistance(byte )

Esta função é destinada à funcionalidade de condução autónoma e permite definir a distância à qual o robô para. Quando encontra um obstáculo.

Por defeito a distância é 9cm. O número especificado de 0 a 255 é interpretado em centímetros,

- Void begin()

Esta função necessita de ser executada uma vez para iniciar a biblioteca e configurar os pinos e periféricos usados.

- Void beginAutoDrive()

Esta função é destinada à funcionalidade de condução autónoma e necessita de ser chamada uma vez para configurar as interrupções associadas aos sensores S2, S3, S4 e CLP. Quando esta função for chamada o robô irá verificar qual o valor de PWM mínimo para colocar ambas as rodas em movimento.

- Void endAutoDrive()

Esta função é destinada à funcionalidade de condução autónoma e necessita de ser chamada uma vez para desassociar as interrupções previamente configuradas pela função beginAutoDrive().

- byte autoDrive(byte)

Esta função é destinada à funcionalidade de condução autónoma e necessita de ser chamada constantemente para efetuar várias tarefas.

Os valores devolvidos são os seguintes:

- “0”, nada a reportar;
- “1”, múltiplas linhas encontradas;
- “2”, obstáculo encontrado;
- “3”, não foram encontradas quaisquer linhas.

O valor inserido é a instrução a efetuar para quando é encontrada mais que uma linha ou algum obstáculo:

- “1”, rodar para a direita;
- “2”, rodar para a esquerda;
- “3”, se não houver obstáculo seguir em frente;
- “4”, retroceder.
- void disableCLP()

Esta função é destinada à funcionalidade de condução autónoma, necessita de ser chamada uma vez para ignorar as leituras do sensor CLP.

- void disableNear()

Esta função é destinada à funcionalidade de condução autónoma e necessita de ser chamada uma vez para ser ativada. A sua função é desativar a leitura do sensor Near.

- void disableUltrasonic()

Esta função é destinada à funcionalidade de condução autónoma, necessita de ser chamada uma vez para ignorar as leituras do sensor de ultrassons HC-SR04.

- void noLineDelay(uint )

Esta função é destinada à funcionalidade de condução autónoma. A sua função é especificar o tempo que o robô demora a parar após deixar de detetar qualquer linha. Por defeito o valor é 700ms, o valor inserido é interpretado em milissegundos.

- void setSpeeds(byte ,byte ,byte)

Esta função permite definir o valor dutty-cycle (8 bits) usado para as velocidades máxima, média e mínima respetivamente. Por defeito os valores usados são 255, 200 e 180.

- byte distance()

Esta função devolve o valor medido (em centímetros) pelo sensor de ultrassons HC-SR04. Devolve um valor entre (e incluindo) 0 a 255.

- void turnLeft(uint16_t )

Esta função permite fazer o robô rodar x graus para a esquerda.

Se for enviado um 0 o robô irá tentar rodar 90 graus. Se for enviado um valor acima de 360 o robô irá apenas rodar 360 graus.

Esta função irá ser efetuada usando a velocidade mínima necessária para mover as rodas, isto para evitar que uma (ou ambas) as rodas derrapem.

Quando esta função for chamada o robô irá verificar qual o valor de PWM mínimo para colocar ambas as rodas em movimento.

- void turnRight(uint16_t )

Esta função permite fazer o robô rodar x graus para a direita.

Se for enviado um 0 o robô irá tentar rodar 90 graus. Se for enviado um valor acima de 360 o robô irá apenas rodar 360 graus.

Esta função irá ser efetuada usando a velocidade mínima necessária para mover as rodas, isto para evitar que uma (ou ambas) as rodas derrapem.

Quando esta função for chamada o robô irá verificar qual o valor de PWM mínimo para colocar ambas as rodas em movimento.

- void steerLeft(byte )

Esta função faz com que o robô vire ligeiramente à esquerda sem parar de seguir em frente.

- void steerRight(byte )

Esta função faz com que o robô vire ligeiramente à direita sem parar de seguir em frente.

- void rotateLeft(byte )

Esta função faz o robô rodar para a esquerda com a velocidade determinada pelo Duty-Cycle (Modelação de Largura de Pulso) inserido. Um valor Duty-Cycle muito baixo pode não ser suficiente para iniciar o movimento.

- void rotateRight(byte )

Esta função faz o robô rodar para a direita com a velocidade determinada pelo Duty-Cycle (Modelação de Largura de Pulso) inserido. Um valor Duty-Cycle muito baixo pode não ser suficiente para iniciar o movimento.

- void stopMotors()

Esta função simplesmente para ambos os motores.

- void forward(byte )

Faz o robô seguir em frente com a velocidade determinada pelo Duty-Cycle (Modelação de Largura de Pulso) inserido. Um valor Duty-Cycle muito baixo pode não ser suficiente para iniciar o movimento. Se o valor inserido for 0 o robô irá parar.

- void reverse(byte )

Faz o robô recuar com a velocidade determinada pelo Duty-Cycle (Modelação de Largura de Pulso) inserido. Um valor Duty-Cycle muito baixo pode não ser suficiente para iniciar o movimento. Se o valor inserido for 0 o robô irá parar.

- void leftWheel(short )

Esta função controla o motor esquerdo individualmente. Pode ser inserido um valor de -255 a 255, um valor negativo fará a roda esquerda recuar e vice-versa. Se for inserido o valor 0 o motor irá parar.

- void rightWheel(short )

Esta função controla o motor direito individualmente. Pode ser inserido um valor de -255 a 255, um valor negativo fará a roda direita recuar e vice-versa. Se for inserido o valor 0 o motor irá parar.

- void clearEncoderCount()

A contagem dos pulsos lidos pelos encoder óticos é feita por hardware usando um módulo do ESP32 denominado “Pulse Counter”, esta função coloca a contagem de ambos os encoder a zero.

- int16_t getLeftEncoderCount()

Esta função devolve o número de pulsos contados pelo encoder esquerdo.

- int16_t getRightEncoderCount()

Esta função devolve o número de pulsos contados pelo encoder direito.

- byte checkSensors()

Esta função efetua uma leitura digital de cada pino presente na placa de sensores IR na frente do robô. Devolve um byte cujos bits significam o seguinte:

  - bit 0: É “1” se o sensor "Near" detetar algo.
  - bit 1: É “1” se o botão CLP for pressionado, isto normalmente acontece quando o robô colide com algo.
  - bit 2: É “1” se o sensor mais à direita detetar uma linha.
  - bit 3: É “1” se o sensor se o sensor da direita detetar uma linha.
  - bit 4: É “1” se o sensor do meio detetar uma linha.
  - bit 5: É “1” se o sensor da esquerda detetar uma linha.
  - bit 6: É “1” se o sensor mais à esquerda detetar uma linha.
- bool readS1 (); bool readS2(); bool readS3; bool readS4(); bool readS5();

Permite ler o estado dos sensores S1, S2, S3, S4 e S5. Devolve o valor “0” se for detetada uma linha preta.

- bool readNear();

Devolve 1 se for detetado um obstáculo pelo sensor Near;

- bool readCLP();

Devolve o valor “1” se o botão (switch) for pressionado.

- Void enSpeedAdj();

Ativa a função de ajuste de velocidade das rodas com base na velocidade especificada, seja esta em em rotações por segundo (RPS), rotações por minuto (RPM) ou metros por segundo (M/S), pelo utilizador.

- Float getRightRPS();

Devolve um valor de tipo float que representa a velocidade da roda direita em rotações por segundo.

- Float getLeftRPS();

Devolve um valor de tipo float que representa a velocidade da roda esquerda em rotações por segundo.

- Float getRightRPM();

Devolve um valor de tipo float que representa a velocidade da roda direita em rotações por minuto.

- Float getLeftRPM();

Devolve um valor de tipo float que representa a velocidade da roda esquerda em rotações por minuto.

- Float getRightMS();

Devolve um valor de tipo float que representa a velocidade da roda direita em metros por segundo.

- Float getLeftMS();

Devolve um valor de tipo float que representa a velocidade da roda esquerda em metros por segundo.

- Void forwardRPS(float );

Permite colocar o robô a mover-se em frente à velocidade especificada (em rotações por segundo RPS).

- Void reverseRPS(float );

Permite colocar o robô a retroceder à velocidade especificada (em rotações por segundo RPS).

- Void rotateRightRPS(float );

Permite colocar o robô a rodar para a direita (sentido horário) à velocidade especificada (em rotações por segundo RPS).

- Void rotateLeftRPS(float );

Permite colocar o robô a rodar para a esquerda (sentido anti-horário) à velocidade especificada (em rotações por segundo RPS).

- Void forwardRPM(float );

Permite colocar o robô a mover-se em frente à velocidade especificada (em rotações por minuto RPM).

- Void reverseRPM(float );

Permite colocar o robô a retroceder à velocidade especificada (em rotações por minuto RPM).

- Void rotateRightRPM(float );

Permite colocar o robô a rodar para a direita (sentido horário) à velocidade especificada (em rotações por minuto RPM).

- Void rotateLeftRPM(float );

Permite colocar o robô a rodar para a esquerda (sentido anti-horário) à velocidade especificada (em metros por segundo m/s).

- Void forwardMS(float );

Permite colocar o robô a mover-se em frente à velocidade especificada (em metros por segundo m/s).

- Void reverseMS(float );

Permite colocar o robô a retroceder à velocidade especificada (em metros por segundo m/s).

- Void rotateRightMS(float );

Permite colocar o robô a rodar para a direita (sentido horário) à velocidade especificada (em metros por segundo m/s).

- Void rotateLeftMS(float );

Permite colocar o robô a rodar para a esquerda (sentido anti-horário) à velocidade especificada (em metros por segundo m/s).

- Void moveAt(byte, byte, float);

Função responsável por colocar o robô em movimento para a direção e velocidade especificadas.

O primeiro parâmetro (da esquerda para a direita) é a direção, podem ser enviados os seguintes valores:

    - “1”, coloca o robô a seguir em frente;
    - “2”, coloca o robô a rodar para a direita;
    - “3”, coloca o robô a recuar;
    - “4”, coloca o robô a rodar para a esquerda;
    - Um valor diferente que se encontre de 0 a 255 irá parar ambos os motores.

O segundo parâmetro especifica o tipo de unidade, podem ser enviados os seguintes valores:

    - “1”, em rotações por segundo (RPS);
    - “2”, em rotações por minuto (RPM);
    - “3”, em metros por segundo (M/S).

O terceiro parâmetro é a velocidade relativa à unidade especificada no segundo parâmetro.

# Esquema elétrico recomendado

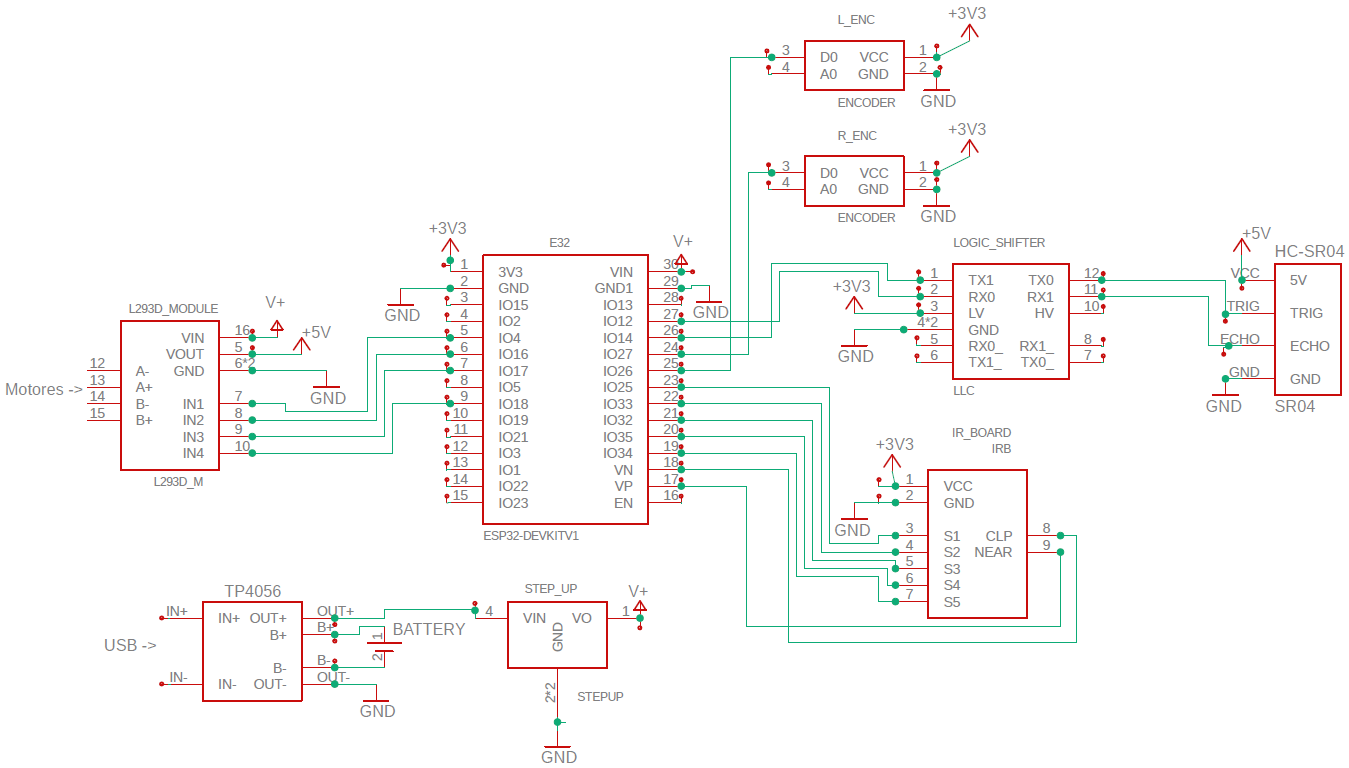
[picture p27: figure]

Figura 0.1 – Esquema

O esquema demonstrado na Figura 0.1 indica o esquema elétrico recomendado para o bom funcionamento do robô didático.

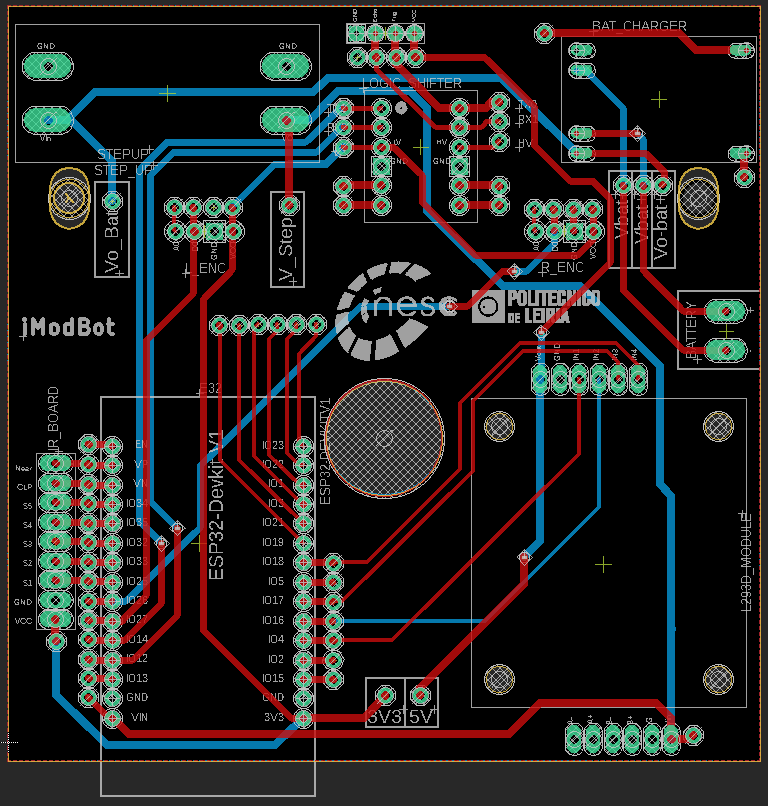
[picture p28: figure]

Figura 0.2 - Placa de Circuito Impresso

A Figura 0.2 exemplifica um possível layout da placa de circuito impresso criada a partir do esquema da Figura 0.1.

# Descrição do funcionamento da condução autónoma da biblioteca

Para efetuar a tarefa de seguir um trajeto de forma autónoma a biblioteca “RobotOnLine” recorre a duas funções principais, sendo uma delas associada a várias interrupções externas.

Função”think()”

A função think() é executada sempre que houver uma interrupção externa nos pinos conectados aos sensores S2, S3, S4 e CLP. Esta função, quando executada, desativa temporariamente as interrupções externas de modo a poder operar sem o risco de ocorrer um “loop” indeterminado.

Resumidamente a função “_think()” verifica se o robô embateu e a posição do trajeto (linha). Se não for encontrada nenhuma linha esta função irá copiar o valor da função “millis()” (esta função devolve o valor em milissegundos decorrido desde o inicio do programa) para uma variável global. Esta variável global será usada como uma “flag” e o valor da mesma será usado pela função “byte autoDrive(byte )” para parar o movimento do robô após um delay especificado. Quando o robô efetua uma curva poderão existir breves momentos em que a linha não seja detetada por nenhum dos sensores, daí a existência deste atraso na paragem do robô.

A função “_think()” também verifica se o robô chegou a um cruzamento. Para tal é que uma das seguintes combinações de sensores seja cumprida:

- S3 e S1 e S2 (sensores do meio e da esquerda);
- S3 e S4 e S5 (sensores do meio e da direita);
- S1 e S2 e S4 e S5 (sensores da direita e da esquerda).

Basicamente os sensores das bordas da placa são verificados de modo a ter a certeza de que o robô se encontra num cruzamento. Este processo foi implementado de modo que o utilizador possa especificar o que o robô deve fazer quando este chega a um cruzamento.

A função “_think()” recorre a uma variável global denominada “_LLP” (abreviado de Last Line Position) para saber a ultima posição da linha, para evitar repetir instruções e para passar informação à função “byte autoDriver(byte )”.

Função “byte autoDrive(byte )”

A função “byte autoDrive(byte )” deve ser chamada o mais brevemente possível, pois esta é complementar à função “_think()” e executa várias tarefas. Esta função recebe e devolve valores, os valores devolvidos têm o seguinte significado:

- “0”, nada a reportar;
- “1”, múltiplas linhas encontradas;
- “2”, obstáculo encontrado;
- “3”, não foram encontradas linhas.

Caso seja encontrado um obstáculo ou múltiplas linhas (valor devolvido “1” ou “2”) podem ser enviados os seguintes valores para a função:

- “1”, o robô irá rodar para a direita até encontrar uma linha;
- “2”, o robô irá rodar para a esquerda até encontrar uma linha;
- “3”, caso não haja nenhum obstáculo, seguir em frente;
- “4”, retroceder.

É necessário enviar sempre um valor para a função, caso não seja intenção do utilizador dar uma instrução ao robô recomenda-se que envie o valor “0”. Apenas os números 1, 2, 3 e 4 dão instruções ao robô, qualquer outro número (até 255) não terá nenhum efeito.

A leitura dos sensores de ultrassons (HC-SR04) e sensor de infravermelho (Near) é efetuada nesta função.

A função “byte autoDrive(byte )” é responsável por fazer o ajuste da velocidade das rodas do robô, esta operação decorre de acordo com o seguinte fluxograma:

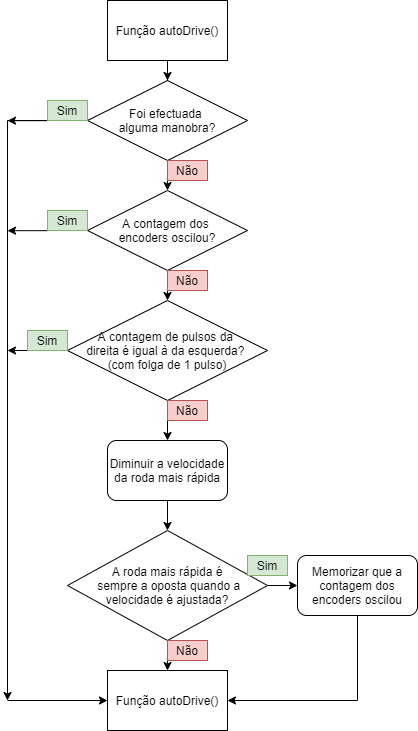
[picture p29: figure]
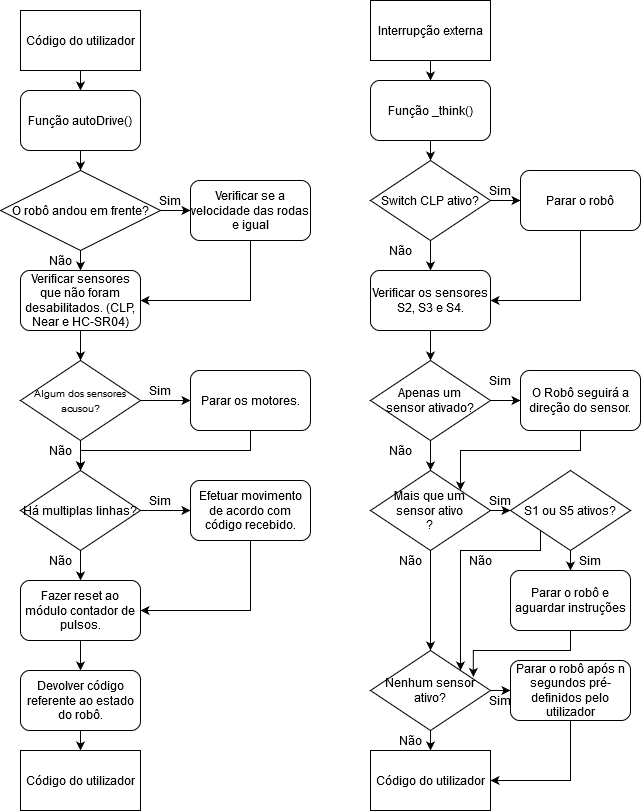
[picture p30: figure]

O seguinte fluxograma descreve o funcionamento de ambas as funções:

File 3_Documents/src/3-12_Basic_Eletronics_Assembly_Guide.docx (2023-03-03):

GUIA BASICA DE MONTAGEM DE CIRCUITOS ELETRICOS

O que é um circuito elétrico?

Em termos simples, é um caminho fechado pelo qual circula uma corrente elétrica numa mesma direção e de forma ordenada.

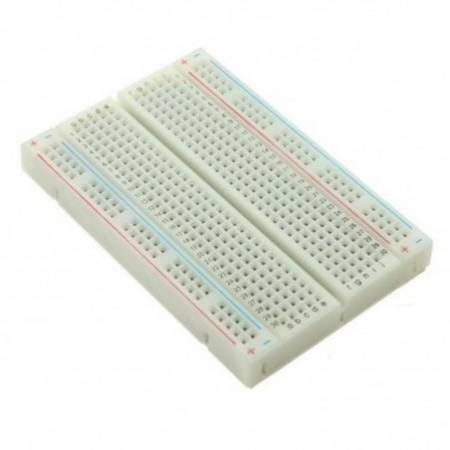
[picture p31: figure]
Placa ensaios Breadboard de 400 pontos

Um circuito elétrico pode estar composto por vários componentes e elementos, alguns mais necessários que outros, como a fonte de tensão, a massa e os cabos. O funcionamento de determinado circuito vai depender em grande medida dos componentes a utilizar.

Breadboard típica

A montagem dos circuitos vai ser numa breadboard, conhecida também por outros nomes como protoboard ou placa de ensaios. A placa tem pequenos furos ou orifícios os quais estão ligados entre si por conexões condutoras. É um componente bastante simples de usar e que permite-nos montar e desmontar uma amplia diversidade de circuitos com facilidade.

É importante conhecer e perceber a direção na qual os componentes devem ser ligados porque caso contrário arriscamo-nos em cometer erros que vão impedir que o circuito funcione como deve ser. Os cabos condutores, que bem podem ser de cobre, fósforo ou estanho, vão estar distribuídos basicamente da seguinte maneira, segundo o patrão típico duma protoboard como a antes indicada. As linhas verticais são chamadas de buses na breadboard e vão representar as o positivo e o negativo, que em geral, se o utilizador o achar conveniente, ao positivo como a fonte de tensão e ao negativo como massa ou terra. As linhas horizontais são o campo onde vamos fazer as ligações dos circuitos e funcionam basicamente da seguinte maneira: uma linha horizontal representa o mesmo nó, pelo qual se juntarmos dois fios no mesmo ponto da linha, vai significar que estão ligados entre si. Se fizermos ao contrário, é dizer, ligar um fio num ponto da horizontal e outro numa linha horizontal diferente, estes não vão estar ligados entre si.

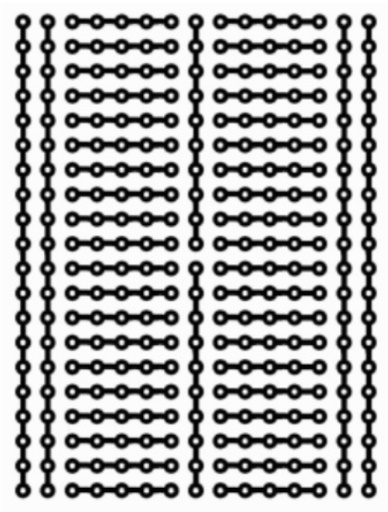
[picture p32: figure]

Uma sugestão ao momento de armar o circuito seria fazê-lo de forma organizada, com fios pequenos, evitando fiação aérea pois resulta mais confuso de perceber em circuitos mais complexos.

Circuitos Elétricos Básicos

- Ligação Serie

Uma ligação série basicamente segue um mesmo caminho para a passagem de corrente. No seguinte exemplo temos três resistências ligadas em serie com uma fonte de tensão. As setas representam a corrente que percorre um único caminho.

Cada um dos números apresentados na imagem a seguir, representa uma linha de pontos como está apresentado na figura de montagem de circuito, assim fazemos uma ligação em serie.

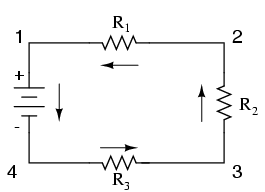
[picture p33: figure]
Circuito resistivo en serie - Análisis de circuitos I

Esquema de circuito serie

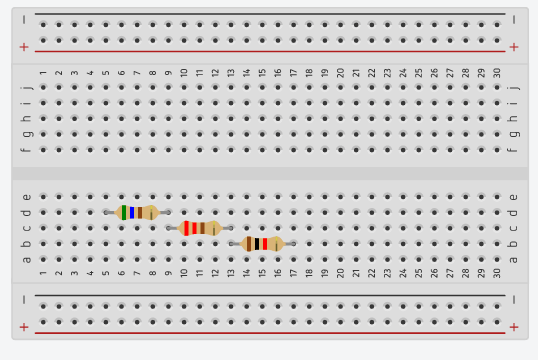
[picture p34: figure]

Montagem de circuito serie

Exemplos:

Neste caso, temos um circuito com quatro diodos led e uma resistência em serie alimentados por uma bateria.

Exemplo de ligação de resistências em série

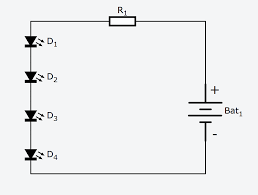
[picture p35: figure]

Esquema de circuito serie Circuito série na breadboard

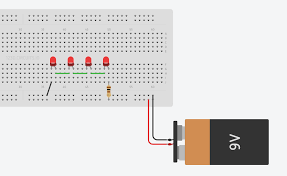
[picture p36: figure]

Ligação Paralelo

Uma ligação em paralelo consiste em que os componentes elétricos coincidam em cada um dos seus extremos, é dizer, a sua saída com a sua saída e a sua entrada com a sua entrada.

Como podemos ver no esquema de circuito paralelo, partilham um ponto numa parte das três diferentes resistências, e outro ponto diferente para a outra parte das três resistências. Como podemos ver na imagem da montagem de circuito paralelo estão ligadas três resistências numa mesma linha de pontos para a parte de acima do circuito e outra diferente linha de pontos para a outra parte das resistências.

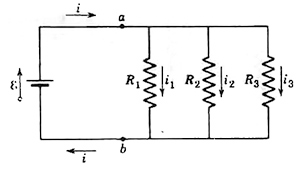
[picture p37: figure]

Esquema de circuito paralelo

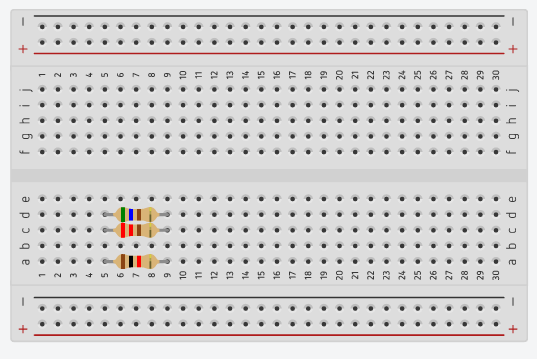
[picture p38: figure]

Montagem de circuito paralelo

Exemplos:

Neste caso, temos uma ligação paralela de 3 diodos LED com 3 resistências de proteção, na primeira imagem temos o esquema e na segunda temos a ligação na protoboard, como podemos ver, partilham uma linha de pontos interligados com fios e não diretamente, mas é indiferente para a perfeita execução do circuito.

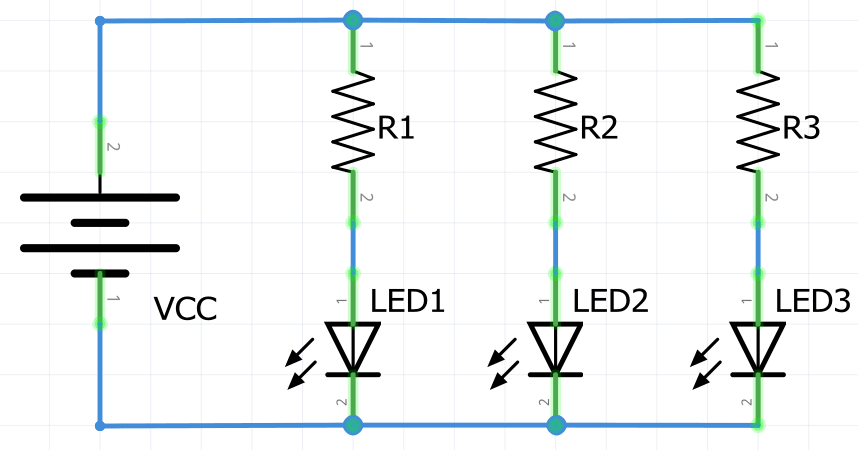
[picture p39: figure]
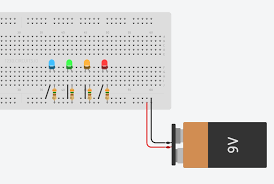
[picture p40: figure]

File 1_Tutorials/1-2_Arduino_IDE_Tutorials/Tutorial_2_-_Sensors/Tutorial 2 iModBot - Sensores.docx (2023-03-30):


| Tutorial – Movimento iModBot@ipleiria.pt

# Introdução

O robô iModBot é um veículo elétrico de pequenas proporções controlado pelo microcontrolador ESP32. Este microcontrolador pode ser programado usando a linguagem C/C++ e o software gratuito Arduino IDE.

Este tutorial vai focar-se na leitura dos vários sensores do robô.

O robô possui os seguintes tipos de sensores:

- Ultrassons, para detetar obstáculos distantes;
- Fim de curso, para detetar uma colisão;
- Sensores infravermelho (IR), para detetar um percurso (Linha preta desenhada numa superfície branca) e também para detetar obstáculos a curta distância;
- Encoder óticos, para obter um feedback da posição das rodas.

นาย arduino: ใช้ Arduino ติดต่อกับ Ping Ultrasonic Sensor ...

O sensor de ultrassons devolve uma distância à qual se encontra um obstáculo. Esta informação será útil para evitar que o robô colida com um obstáculo.

Ligações deste módulo:

Echo | D14
Trig | D12

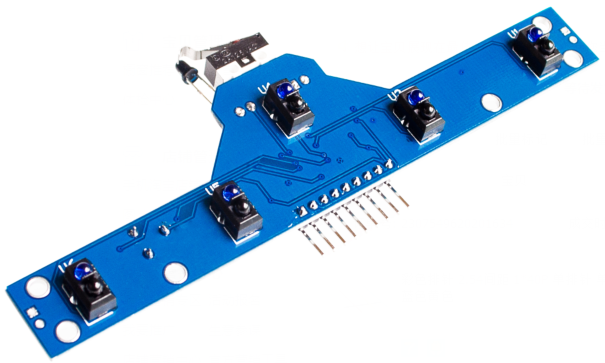
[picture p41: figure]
Jual Produk Module Tcrt5000 5 Channel Line Murah dan Terlengkap ...

O sensor fim de curso é um botão (switch, denominado CLP) colocado na parte da frente do módulo de sensores IR.

Os dois LED emissor e recetor infravermelho, denominado sensor “Near”, acima do switch permitem detetar obstáculos a curta distância, a luz natural poderá causar leituras erradas no recetor infravermelho.

Os cinco sensores infravermelho na parte inferior da placa, denominados S1, S2, S3, S4 e S5, permitem detetar uma linha preta numa superfície clara (branca).

Ligações deste módulo:

S1 | D25
S2 | D33
S3 | D32
S4 | D35
S5 | D34
CLP | VN ou D39
Near | VP ou D36

Motor Speed Encoder Sensor | Open ImpulseOpen Impulse

Os sensores/encoder óticos servem para obter um feedback da rotação das rodas podendo deste modo obter a distância percorrida e saber se uma está a rodar mais rapidamente que a outra.

Ligações deste módulo:

Encoder da roda esquerda | D0 | D26
Encoder da roda direita | D0 | D27

Deve haver uma peça semelhante a esta no eixo da roda:

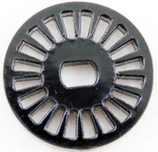
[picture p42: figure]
Photoelectric Encoder Disc For Motor Speed Measurement, मोटर ...

Esta peça permite ao encoder fazer a contagem dos pulsos da roda. Cada vez que uma roda dá uma volta completa (360º) a contagem deve aumentar 40 pulsos.

A contagem dos pulsos aumenta sempre, independentemente da direção em que as rodas se deslocam.

O número de pulsos também pode ser usado para calcular a distância percorrida pela roda, para tal precisamos de medir o diâmetro (d) da roda. Após sabermos o diâmetro vamos calcular o perímetro (P) usando a fórmula P = π * d. Após conhecermos o perímetro sabemos que 40 pulsos equivalem ao perímetro calculado, desta forma a distância percorrida (D) pode ser calculada da seguinte maneira:

D=(pulsos * P)/40 em que P é o perímetro da roda, “pulsos” o número de pulsos contados e D a distância percorrida.

Ex1 - Usar sensor de ultrassons com a biblioteca
Descrição Este exemplo obter a distância, em cm, à qual se encontra um obstáculo e apresentar a mesma no monitor série. Sintaxe Distance(); = devolve o valor, em cm, da distancia medida. Parâmetros Nenhum Respostas Nenhum | Exemplo: #include <iModBot.h> iModBot robot; void setup() { robot.begin(); Serial.begin(115200); } void loop() { byte dist = robot.distance(); Serial.print(Distancia (cm): ); Serial.println(dist); delay(250); }

Ex2 - Ler sensor CLP, Near, S1, S2, S3, S4 e S5

#### Descrição

Este exemplo permite obter o estado de cada pino o apresentar o mesmo no monitor série.

#### Sintaxe

readCLP();

readNear();

#### readS1();

readS2();
readS3();
readS4();
readS5();

#### Parâmetros

state = variável que recebe o valor da função, 1 ou 0, consoante o estado do pino.

#### Respostas

Nenhum

Exemplo:

#include <iModBot.h>

iModBot robot;

void setup()

{

robot.begin();

Serial.begin(115200);

}

void loop()

{

bool state = 0;

state = robot.readCLP();

Serial.print("Estado do pino CLP: ");

Serial.println(state);

state = robot.readNear();

Serial.print("Estado do pino Near: ");

Serial.println(state);

state = robot.readS1();

Serial.print("Estado do pino S1: ");

Serial.println(state);

state = robot.readS2();

Serial.print("Estado do pino S2: ");

Serial.println(state);

state = robot.readS3();

Serial.print("Estado do pino S3: ");

Serial.println(state);

state = robot.readS4();

Serial.print("Estado do pino S4: ");

Serial.println(state);

state = robot.readS5();

Serial.print("Estado do pino S5: ");

Serial.println(state);

delay(250);

}

Ex3 - Ler e reiniciar a contagem de pulsos dos encoders.
Descrição Este exemplo permite ler o número de pulsos contados pelos encoders óticos e apresentar os mesmos no monitor série. Sintaxe getLeftEncoderCount();/* devolve um número de pulsos contados pelo Encoder da roda esquerda */ getRightEncoderCount(); /* devolve um número de pulsos contados pelo Encoder da roda direita */ clearEncoderCount(); /* coloca a contagem de pulsos a zero */ Parâmetros Nenhum Respostas “short” é um tipo de variável com metade do tamanho da variável de tipo “int”. | Exemplo: #include <iModBot.h> iModBot robot; short leftPulse = 0; short rightPulse = 0; void setup() { robot.begin(); Serial.begin(115200); } void loop() { leftPulse = robot.getLeftEncoderCount(); rightPulse = robot.getRightEncoderCount(); Serial.print("Pulso da roda esquerda: "); Serial.print(leftPulse); Serial.print("\t"); Serial.print("Pulso da roda direita: "); Serial.println(rightPulse); if( (leftPulse > 10000) || (rightPulse > 10000) ) { robot.clearEncoderCount(); } delay(250); }

Tutorial – Movimento iModBot@ipleiria.pt Página 30 de 30

Politécnico de Leiria 2019/2020

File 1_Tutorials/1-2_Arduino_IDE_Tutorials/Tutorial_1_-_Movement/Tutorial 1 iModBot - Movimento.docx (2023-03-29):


| Tutorial – Movimento iModBot@ipleiria.pt

# Introdução

O robô iModBot é um veículo elétrico de pequenas proporções controlado pelo microcontrolador ESP32. Este microcontrolador pode ser programado usando a linguagem C/C++ e o software gratuito Arduino IDE.

Este tutorial vai focar-se no movimento do robô.

O robô possui duas rodas que lhe permitem mover em qualquer direção. Cada roda possui um motor elétrico cuja direção é controlada pela sua polarização.

Este motor é conectado ao módulo L293D como descrito no guia de montagem:


O controlo dos motores é efetuado diretamente pelo circuito integrado L293D, sendo este controlado pelo microcontrolador ESP32. A velocidade de cada roda é controlada por modulação de largura de pulso (PWM).

São usados dois pinos para controlar cada motor, sendo assim usados quatro pinos no total para o controlo das duas rodas.

Estes quatro pinos, geralmente, podem ser qualquer GPIO (General Purpose Input Output). Cada módulo de desenvolvimento baseado no microcontrolador ESP32 possui pinos (GPIO) restritos e pinos disponíveis diferentes.

O módulo que é enviado juntamente com o kit iModBot é denominado “DOIT ESP32 DevKit V1”. Se for usada a biblioteca “RobotOnLine_Rev2” por defeito os pinos destinados ao controlo das rodas serão:

- GPIO 4 e GPIO 16, para a roda direita;
- GPIO 17 e GPIO 18, para a roda esquerda.

Número do GPIO: | Estado lógico: | Efeito:
4 | 1 | Motor direito recua.
16 | 0
4 | 0 | Motor direito avança.
16 | 1
17 | 1 | Motor esquerdo avança.
18 | 0
17 | 0 | Motor esquerdo recua.
18 | 1

Usando as funções proporcionadas pelo ambiente Arduíno um estado lógico “1” pode ser causado no pino “4” usando “digitalWrite(4, HIGH);”, da mesma maneira um estado lógico “0” pode ser causado usando “digitalWrite(4, LOW);”.

Para parar um motor é necessário colocar ambos os pinos no estado lógico “0”.

Para poder controlar a velocidade a que o motor gira é apenas necessário substituir o estado lógico “1”, indicado na tabela acima, por um sinal PWM.

A biblioteca “RobotOnLine_Rev2” usa, por defeito, os seguintes parâmetros para o sinal PWM:

- Frequência de 5kHz.
- Resolução de 8 bits.

Ex 1 - Controlo do movimento simples.

#### Descrição

Este exemplo permite mover o robô em qualquer direção sem controlo da velocidade.

#### Sintaxe

digitalWrite(pino, estado);

#### Parâmetros

pino //número associado ao pino

estado //HIGH ou LOW

#### Respostas

Nenhum

### Exemplo:

void setup()

{

pinMode( 4,OUTPUT); //Direita

pinMode(16,OUTPUT); //Direita

pinMode(17,OUTPUT); //Esquerda

pinMode(18,OUTPUT); //Esquerda

}

void loop()

{

// Para seguir em frente

digitalWrite( 4, LOW);

digitalWrite(16, HIGH);

digitalWrite(17, HIGH);

digitalWrite(18, LOW);

delay(1000);

// Para recuar

digitalWrite( 4, HIGH);

digitalWrite(16, LOW);

digitalWrite(17, LOW);

digitalWrite(18, HIGH);

delay(1000);

// Rodar para a direita

digitalWrite( 4, HIGH);

digitalWrite(16, LOW);

digitalWrite(17, HIGH);

digitalWrite(18, LOW);

delay(1000);

// Rodar para a esquerda

digitalWrite( 4, LOW);

digitalWrite(16, HIGH);

digitalWrite(17, LOW);

digitalWrite(18, HIGH);

delay(1000);

//Parar os motores

digitalWrite( 4, LOW);

digitalWrite(16, LOW);

digitalWrite(17, LOW);

digitalWrite(18, LOW);

delay(1000);

}

Ex 2 - Controlo usando a biblioteca
Descrição Permite controlar o movimento do robô em qualquer direção e também o controlo da velocidade das rodas. Sintaxe forward(velocidade ); reverse(velocidade); rotateLeft(velocidade); rotateRight(velocidade): stopMotors(); Parâmetros Velocidade = é um número de 0 a 255. Respostas O número de bytes disponíveis para serem lidos | Exemplo: #include <iModBot.h> iModBot robot; void setup() { robot.begin(); } void loop() { // Velocidade // Pode variar de 1 a 255 byte speed = 255; // Para seguir em frente robot.forward(speed); delay(500); // Para recuar robot.reverse(speed); delay(500); // Rodar para a direita robot.rotateRight(speed); delay(500); // Rodar para a esquerda robot.rotateLeft(speed); delay(500); // Parar os motores robot.stopMotors(); delay(1000); }

## Ex 3 - Controlo individual de cada roda usando a biblioteca

Descrição Neste exemplo é possível controlar individualmente a direção de cada roda. Sintaxe rightWheel(velocidade ); leftWheel(velocidade ); Parâmetros - Velocidade = número de -255 a 255, um valor negativo faz a roda recuar e vice-versa. Um 0 faz a roda parar. Respostas Nada | Exemplo: #include <iModBot.h> iModBot robot; void setup() { robot.begin(); } void loop() { // Mover roda esquerda em frente robot.leftWheel(255); delay(1000); // Mover roda esquerda para trás robot.leftWheel(-255); delay(1000); // Mover roda direita em frente robot.rightWheel(255); delay(1000); // Mover roda direita para trás robot.rightWheel(-255); delay(1000); }

## Ex 4 - Rodar o robô “n” degraus usando a biblioteca

Descrição Neste exemplo é possível rodar o robô “n” graus e escolher para que lado o mesmo deve rodar (esquerda ou direita). Sintaxe turnLeft (graus); turnRight (graus); Parâmetros - Graus = é um número de 1 a 360 que corresponde a quantos graus o robô irá rodar. Um 0 faz o robô rodar 90 graus. Respostas Nada | Exemplo: #include <iModBot.h> iModBot robot; void setup() { robot.begin(); } void loop() { // Rodar para a esquerda 90 graus robot.turnLeft(90); delay(1000); // Rodar para a direita 270 graus robot.rightWheel(270); delay(1000); }

## Ex 5 - Controlar velocidade e movimento sem biblioteca

#### Descrição

Este exemplo permite controlar o movimento do robô sem recurso à biblioteca “RobotOnLine_Rev2”.

#### Sintaxe

ledcSetup(canalPWM, frequenciaPWM, resoluçãoPWM);

ledcWrite(canalPWM, PWM);

#### Parâmetros

canalPWM = canal PWM de 0 a 15.

frequenciaPWM = frequência de 1 Hz a 312.5kHz

resoluçãoPWM = resolução do pulso PWM

PWM = largura do pulso PWM (8 bits, 0 a 255 neste caso)

#### Returns

#### Exemplo:

#define PWM_Frequency 5000 // PWM frequency, up to 312.5kHz

#define _IN1_PWM_channel 0 // select the channel number

#define _IN2_PWM_channel 1 // there are 15 channels,

#define _IN3_PWM_channel 2 // choose between 0 to 15

#define _IN4_PWM_channel 3 // (not related to the pins)

#define PWM_RESOUTION 8 // 8 bits

//motor pins IN1&IN2 right engine

byte _IN1 = 4; //IO15 and 5 are HIGH during boot.

byte _IN2 = 16;

//IN3&IN4 left engine

byte _IN3 = 17;

byte _IN4 = 18;

void setup()

{

pinMode(4,OUTPUT);

pinMode(16,OUTPUT);

pinMode(17,OUTPUT);

pinMode(18,OUTPUT);

//setup PWM for motor pins

ledcSetup(_IN1_PWM_channel, PWM_Frequency, PWM_RESOUTION);

ledcAttachPin(_IN1, _IN1_PWM_channel);

ledcSetup(_IN2_PWM_channel, PWM_Frequency, PWM_RESOUTION);

ledcAttachPin(_IN2, _IN2_PWM_channel);

ledcSetup(_IN3_PWM_channel, PWM_Frequency, PWM_RESOUTION);

ledcAttachPin(_IN3, _IN3_PWM_channel);

ledcSetup(_IN4_PWM_channel, PWM_Frequency, PWM_RESOUTION);

ledcAttachPin(_IN4, _IN4_PWM_channel);

ledcWrite(_IN1_PWM_channel, 0);

ledcWrite(_IN2_PWM_channel, 0);

ledcWrite(_IN3_PWM_channel, 0);

ledcWrite(_IN4_PWM_channel, 0);

}

void loop()

{

byte speed = 255;

// move forward

//right engine forward

ledcWrite(_IN1_PWM_channel, 0);

ledcWrite(_IN2_PWM_channel, speed);

//left engine forward

ledcWrite(_IN3_PWM_channel, speed);

ledcWrite(_IN4_PWM_channel, 0);

delay(1000);

// turn left

//right engine forward

ledcWrite(_IN1_PWM_channel, 0);

ledcWrite(_IN2_PWM_channel, speed);

//left engine reverse

ledcWrite(_IN3_PWM_channel, 0);

ledcWrite(_IN4_PWM_channel, speed);

delay(1000);

// turn right

//right engine reverse

ledcWrite(_IN1_PWM_channel, speed);

ledcWrite(_IN2_PWM_channel, 0);

//left engine forward

ledcWrite(_IN3_PWM_channel, speed);

ledcWrite(_IN4_PWM_channel, 0);

delay(1000);

// reverse

//right engine reverse

ledcWrite(_IN1_PWM_channel, speed);

ledcWrite(_IN2_PWM_channel, 0);

//left engine reverse

ledcWrite(_IN3_PWM_channel, 0);

ledcWrite(_IN4_PWM_channel, speed);

delay(1000);

}

Tutorial – Movimento iModBot@ipleiria.pt Página 30 de 30

Politécnico de Leiria 2019/2020

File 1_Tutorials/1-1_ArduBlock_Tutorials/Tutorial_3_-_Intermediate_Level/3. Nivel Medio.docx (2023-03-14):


| Instituto de Engenharia de Sistemas e Computadores (INESC) de Coimbra Tutorial – Nível Médio

Programar o robô iModBot (https://github.com/Guilherme010101/iModBot2)

por blocos


Alunos: Abel Teixeira - 2180522

Samuel Lourenço – 2180356

Docente: Carlos Neves

Luís Conde

Ano letivo: 2019/2020

# Nível Médio (Middle)

No nível médio vai alterar o bloco “Robo OTA” que só contém o loop para o bloco “Basic OTA” que está na aba “Middle level” para se começar a habituar ao modo de programação em C++.


## 1. Blocos do Setup

Os quatro blocos abaixo são colocados no setup para que os blocos do loop funcionem.

### 1.1. Bloco “Robot Library”

Este bloco tem de estar presente em todos os programas feitos no nível médio (Middle) para configurar a biblioteca.

### 1.2. Blocos “Speed Configuration”

Este bloco vai definir a velocidade de 0 a 255 que o robô vai andar.

## 2. Blocos do loop

Como os blocos no setup, vamos passar para o loop aqui conforme montar os blocos vai desenvolvendo o programa que o robô vais desempenhar.

### 2.1. Bloco “Timing”

Ao colocar o bloco “Timing” vai temporizar os segundos que colocar no bloco à frente antes de passar para o próximo bloco.

### 2.2. Bloco “stop before obstacle”

Com este bloco o robô vai andar até que fique a uma distância igual à indicada à frente deste bloco. Quando estiver a essa distância o robô para, esperando por uma nova instrução.

### 2.3. Blocos “Stop the 2 Wheels”, “Left Wheel Stop” e o “Right Wheel Stop”

Os três blocos fazem com que as rodas parem. O bloco “Stop the 2 Wheels” faz parar as duas rodas ao mesmo tempo. O bloco “Left Wheels Stop” faz parar só a roda esquerda e o bloco “Right Wheels Stop” faz parar só a roda direita.

### 2.4. Blocos “Left Wheel Advances” e “Right Wheel Advances”

Os dois blocos fazem com que o robô possa andar para frente. O bloco “Left Wheel Advances” faz com que a roda esquerda ande para a frente e o bloco “Right Wheel Advances” faz o mesmo só que com a roda direita.

### 2.5. Blocos “Left Wheel Recedes” e “Right Wheel Recedes”

Os dois blocos fazem com que o robô recue. O bloco “Left Wheel Recedes” faz com que a roda esquerda ande para atrás e o bloco “Right Wheel Recedes” faz o mesmo só que com a roda direita.

## 3. Exemplo de programas

## 3.1. Andar em frente durante 10 segundos

## No programa em baixo no Setup:

- Bloco “Robot Library” chama a biblioteca;
- Bloco “Speed Configuration” define a velocidade que vai andar o robô;

## No loop:

- Bloco “Run Once” faz com que o programa só corra uma vez;
- Bloco “Left Wheel Advances” aciona a roda esquerda a andar para a frente;
- Bloco “Right Wheel Advances” aciona a roda direita a andar para a frente;
- Bloco “Timing” temporiza as rodas a andar para a frente durante 10 segundos;
- Bloco “Stop the 2 Wheels” desliga as duas rodas.


Durante 10 segundos

## 3.2. Andar à roda

## No programa em baixo no Setup:

- Bloco “Robot Library” chama a biblioteca;
- Bloco “Speed Configuration” define a velocidade que vai andar o robô;

## No loop:

- Bloco “Right Wheel Advances” aciona a roda direita a andar para a frente;
- Bloco “Left Wheel Recedes” aciona a roda esquerda do robô a recuar

Fazendo com que o robô rode para a esquerda sem parar.


Nível Médio – iModBot@ipleiria.pt Página 1 de 7

Politécnico de Leiria 2019/2020

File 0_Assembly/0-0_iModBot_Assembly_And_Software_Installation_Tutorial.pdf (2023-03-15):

## TUTORIAL DE MONTAGEM E INSTALAÇÃO DE SOFTWARE PARA IMODBOT


### INDICE

INTRODUÇÃO | 4

### 1. Instalação de Sowtfares úteis para o robô | 4

### 1.1. Instalação de Arduino IDE | 4

### 1.2. Instalação de bibliotecas para Arduino com funções para o robô | 7

### 1.3. Configuração do Arduíno IDE para programar o ESP32 | 10

### 1.4. Instalação de Ardublocks no Arduíno IDE | 15

### 2. Montagem do iModBot | 21

### 2.1. Componentes | 21

### 2.2. Ligações e montagem | 24

### 2.3. Passos a seguir | 25

### 3. Programar o teu robô | 32

### 3.1. Piscar LED e ligar WiFi | 32

### 3.2. Apagar Bloco | 33

### 3.3. Fazer Círculos | 34

### 3.4. Movimentos aleatórios | 34

### 4. Exemplos |

### TABELA DE FIGURAS

Figura 1 - arduino.cc | 4
Figura 2 - Just Download Arduino IDE | 5
Figura 3 - Obter Arduino IDE | 5
Figura 4 - Iniciar Arduino | 6
Figura 5 - Arduino IDE Instalado | 6
Figura 6 - Descarregar libraries.7z | 7
Figura 7 - Bibliotecas do Arduino | 8
Figura 8 - Copiar Libraries | 8
Figura 9 - Colar libraries | 9
Figura 10 - Arduino com bibliotecas instaladas | 10
Figura 11 - Ficheiro > Preferências | 11
Figura 12 - "Janela Preferências" | 11
Figura 13 | 12
Figura 14 - Link colado | 12
Figura 15 - Janela Preferências configurada | 12
Figura 16 | 13
Figura 17 | 13
Figura 18 | 14

INTRODUÇÃO

Esta guia serve para orientar ao utilizador nos primeiros passos do robô educacional iModBot,

na sua montagem, instalação dos diferentes softwares e na programação e a utilização dos

mesmos.

Esta guia compõe várias componentes importantes do projeto iModBot: montagem e

programação. Mostra também os links com os arquivos e os tutoriais necessários.

1. Instalação de Sowtfares úteis para o robô.

1.1.Instalação de Arduino IDE.

- Carrega no link da página de arduino para descarregar o Arduino IDE.

Link: https://www.arduino.cc/en/software

- No quadro da direita escolhe o sistema operativo do teu computador.

Figura 1 - arduino.cc


- Clicamos em “JUST DOWNLOAD”

Figura 2 - Just Download Arduino IDE

- No Windows 10, clicamos em “Obter”, para assim fazer a descarga do Arduino IDE.

Figura 3 - Obter Arduino IDE

- No caso de Windows 10, será aberto o Microsoft Store e começará a descarga e

instalação de Arduino IDE, e quando estar pronto, clicamos em “Iniciar”, como na

Figura 4, e permitimos os acessos necessários para que seja aberta a janela de

Arduino, e já teremos o Arduino IDE pronto para programar, ao momento de abrir

devemos ter uma janela igual à Figura 5.


Figura 4 - Iniciar Arduino

Figura 5 - Arduino IDE Instalado

O site também possui guias de instalação passo a passo para cada sistema operativo.

Guias de instalação:

- Windows: https://www.arduino.cc/en/Guide/Windows
- Linux: https://www.arduino.cc/en/Guide/Linux
- Mac Os X: https://www.arduino.cc/en/Guide/MacOSX
- Versão portátil (Windows e Linux): https://www.arduino.cc/en/Guide/PortableIDE
- ChromeOs: https://chrome.google.com/webstore/detail/arduino-

create/dcgicpihgkmccjigalccipmjlnjopdfe (https://chrome.google.com/webstore/detail/arduino-create/dcgicpihgkmccjigalccipmjlnjopdfe) (particulares) e

https://create.arduino.cc/plans/chrome-app (educativo)

1.2. Instalação de bibliotecas para Arduino com funções para o robô.

O software Arduino IDE precisa mais de bibliotecas para efetuar funções especificamente criadas para o robô, por isso, é necessário fazer as seguintes alterações do programa.

- Carrega no link apresentado a seguir e descarrega o arquivo comprimido “libraries.7z”, como é apresentado na Figura 6.

Figura 6 - Descarregar libraries.7z

- Após a descarga, descomprime o arquivo até ter uma pasta “libraries”. Abrir a pasta para verificar que se encontram todas as pastas amostradas na Figura 7.


Figura 7 - Bibliotecas do Arduino

- Copiamos a pasta “libraries”. Localizada, geralmente, no endereço amostrado na Figura 8.

Figura 8 - Copiar Libraries

- E colamos na pasta “Arduino” que foi criada automaticamente no momento da instalação de Arduino IDE, geralmente dada no endereço como da Figura 9, que geralmente ao instalar vem vazia por defeito, mas, caso já tenha uma pasta com nome “libraries”, basta substituir a pasta libraries já existente pela pasta descarregada.

Figura 9 - Colar libraries

- Para verificar que já temos instaladas as bibliotecas que precisamos, vamos abrir o Arduíno IDE para colocar exemplos de programação do nosso robô que se encontra nas bibliotecas agora instaladas. Seguimos os comandos mostrados na Figura 10, e caso aparecer as opções que estão assinaladas na Figura 10, é porque fizemos corretamente a instalação das bibliotecas para o robô.


Figura 10 - Arduino com bibliotecas instaladas

1.3.Configuração do Arduíno IDE para programar o ESP32.

Passo muito importante para programar o nosso robô. Ao momento de instalar o Arduino não

é possível programar a placa ESP32, por isso, é necessário fazer configurações importantes

dentro do Arduino IDE para começar a programar o ESP32.

Para isso, devemos seguir os seguintes passos.

- No Arduino IDE, no separador “Ficheiro”, clicamos em “Preferências”.


Figura 11 - Ficheiro > Preferências

- Irá aparecer uma nova janela igual à da Figura 12, onde vamos clicar no quadro igual ao assinalado na Figura 12.

Figura 12 - "Janela Preferências"

- Nesta nova janela que aparecerá ao fazer o passo anterior iremos colar no espaço vazio (Figura 13) o link “https://dl.espressif.com/dl/package_esp32_index.json”, e deverá ficar como na Figura 14 e clicar em “OK”.


Figura 13


Figura 14 - Link colado

- Voltará á janela preferências, mas com o link que colamos na parte “URL Adicionais do Gestor de Placas”, e clicamos em “OK”.

Figura 15 - Janela Preferências configurada

- A seguir, clicamos em “Ferramentas”, depois em “Placa” e finalmente em “Gestor de Placas” como pode-se ver na Figura 16.


Figura 16

- Na janela que aparece na Figura 17, no espaço em branco assinalado escrevemos “ESP32”, seguidamente quando aparecer a opção que é mostrada na Figura 18 procuramos a versão mais recente e seguidamente clicamos em “Instalar”, como é mostrado na Figura 18 e iniciará a instalação para poder programar a placa ESP32 com Arduíno IDE.

Figura 17


Figura 18

- Verificamos que ficou instalado e clicamos em fechar.

Figura 19

- E por último seguimos o caminho de comandos mostrados na Figura 20 que são, “Ferramentas”, seguido de “Placa”, seguido de “ESP32 Arduino” e finalizamos em “ESP32 Dev Module”. E já temos o Arduino IDE configurado para programar a placa ESP32 que funciona como o cérebro do robô.


Figura 20

- O link que vamos disponibilizar é um vídeo que resume os passos caso existi alguma dúvida do processo.

Link: https://www.youtube.com/watch?v=xiqXJj58ynI&ab_channel=SamuelLouren%C3%A7o

1.4.Instalação de Ardublocks no Arduíno IDE

Para programar facilmente o robô vamos utilizar uma ferramenta chamada “Ardublocks”, que permite programar funções no robô com a simples ação de colocar blocos com um ordem específico fará uma ação, ou conjunto de ações, programadas para o robô, e para instalar isto é preciso seguir os seguintes passos.

- No link próximo, descarrega o ficheiro “ardublock-beta-20171028.jar”.

Figura 21 - Descarregar ficheiro

- No Arduíno IDE, em Ficheiro, clicamos em “Preferências”


Figura 22

- Procuramos o endereço amostrado na Figura 23 e nas pastas do seu computador procuramos o endereço da Figura 23 até chegar à pasta como na Figura 24.


Figura 23

Figura 24

- Neste endereço criamos uma pasta com o nome “tools” (Figura 25) e nesta nova pasta criamos uma pasta com o nome “ArduBlockTool” (Figura 26) e nesta pasta criamos mais uma pasta com o nome “tool” (Figura 27).

Figura 25

Figura 26


Figura 27

- E dentro desta última pasta (Figura 27), vamos colar o arquivo descarregado no primeiro passo (Figura 21).

Figura 28

- E pronto, no Arduíno IDE deverá aparecer em “Ferramentas” uma opção chamada “ArduBlock” como na Figura 29. Ao clicar abrirá uma nova janela igual à da Figura 30, e o Arduíno IDE está pronto para programar o robô!


Figura 29

Figura 30

2. Montagem do iModBot.

2.1.Componentes.

Está disponível uma lista com todos os componentes, com uma sugestão ou referência de onde

e a que preço pode o utilizador adquiri-los com várias opção de preços. Também se encontra

uma listagem descritiva dos componentes para ajudar ao utilizar a perceber melhor o seu

funcionamento. É muito importante ter todos os componentes tal como a listagem a seguir.

No próximo link descarrega o ficheiro Excel chamado “Listagem de componentes iModBot + links

de compra auxiliares” onde conseguirás alguns links de compra seguido da listagem completa

dos componentes eletrónicos.

Link:

https://github.com/BelenEJS/iModBot/tree/main/Tutorial%20de%20montagem%20iModBot


Figura 31

A seguir alguns dos componentes que vamos encontrar na listagem de compras, no ponto 2.3

será explicado o funcionamento de cada um dos aparelhos eletrónicos, é dizer, ao momento de

explicar a montagem.

- DOIT ESP32 DevKit V1 – módulo que será responsável pelas comunicações e controlo.

Figura 32 - Placa ESP32

- Módulo de controlo dos motores, L293D

Figura 33 - L293D

- Placa de sensores IR 74HC14

Figura 34 - Placa de sensores

- Encoder Óticos

Figura 35 - Encoder Ótico

- HC-SR04

Figura 36 - HC-SR04

- Módulo de carga TP4056

Figura 37 - TP4056

- Módulo elevador de tensão MT3608

Figura 38 - Módulo elevador de tensão MT3608

- Bateria de lítio de iões, 3.7v, 2500mAh

Figura 39 - Batería

2.2.Ligações e montagem

Estabeleça as ligações como demonstrado nas imagens seguintes. Também está disponível um

vídeo que demonstra a montagem dos vários componentes.

O robô deve ficar no possível na estrutura seguinte, mas no início quando o utilizador esteja a

começar a interagir com o dispositivo pode ir montando tudo numa breadboard de forma

organizada e otimizando o espaço, pois, o robô deve ser especialmente pequeno e deve entrar

na estrutura base com as rodas que se indica em baixo. Se o utilizador é iniciante na área de

circuitos e eletrónica, sugerimos revisar o tutorial de circuitos elétricos e montagem básica de

circuitos, na pasta Tutorial de montagem iModBot.

→ Link do guia básico de montagem de circuitos elétricos para iniciantes:

https://github.com/BelenEJS/iModBot


Figura 40 - Robô montado

Segue os passos do vídeo para ter o teu robô pronto para fazer as tarefas que proponhas, caso

não ficar esclarecido no vídeo como efetuar as ligações dos componentes eletrónicos segue os

passos referidos no ponto 2.3.

Link do vídeo:

https://www.youtube.com/watch?v=i4wFh0GqzkM&feature=emb_logo&ab_channel=AbTx

2.3.Passos a seguir

- Passo 1: ligamos o módulo elevador de tensão MT3608 ao modulo de carga TP4056 e

este à bateria de lítio. Para ligar os dois módulos, devemos ligar o pin Vin+ do modulo

elevador de tensão ao out+ do modulo de carga, e assim também o vin- do elevador de

tensão ao out-. Depois para ligar a bateria, ligamos o pin B+ ao positivo da bateria ou fio

vermelho e o pin B- à terra da bateria ou fio preto.


Figura 41 - Passo 1

- Passo 2: ligar o pin VIN+ modulo elevador de tensão ao ESP32 e ao modulo de controlo

dos motores como mostra-se na Figura 42. Depois ligamos o pin VOUT- ao modulo de

controlo dos motores.

Figura 42 - Passo 2

- Passo 3: ligação dos motores ao modulo de controlo dos motores assim como se

mostra a Figura 43. Estes vão controlar o movimento das rodas direita e esquerda.


Figura 43 - Passo 3

- Passo 4: deve ligar o ESP32 ao modulo de controlo dos motores nos pinos indicados

com as cores seguintes.


Figura 44 - Passo 4

- Passo 5: Para alimentar o sensor de proximidade, é preciso fazer as seguintes ligações.

Figura 45 - Passo 5

- Passo 6: Agora, temos de ligar os pinos do ESP32 ao sensor de proximidade, mas,

primeiro devemos passar pelo canal Bidirecional conversor de deslocador de nível

lógico.

Figura 46 - Passo 6

- Passo 7: Neste passo, vamos alimentar a placa de sensores infravermelhos que servem

para detetar cor preto e cores claras e os dois sensores infravermelhos que servem para

recetar a velocidade das rodas.


Figura 47 - Passo 7

- Passo 8: Agora, vamos ligar dois pinos do ESP32 aos respetivos sensores infravermelhos

de velocidade, é importante ter em conta a roda direita e esquerda, para quando

programar o robô não existir erros, porque às vezes a roda direita não vai ter a mesma

velocidade do que a esquerda ou ao contrário, para fazer curvas, rodar em círculos, etc.

Figura 48 - Passo 8

- Passo 9: E por último, vamos ligar com cabos macho-fêmea, a placa ESP32 para a placa

de sensores infravermelhos, ter em conta as cores para não ligar erradamente, só assim

fazemos que o robô possa seguir linhas pretas ou mais funções.

Figura 49 - Passo 9

3. Programar o teu robô.

Nesta altura, já tens o teu próprio robô armado e os softwares prontos para programar o robô, e para verificar os movimentos do robô, a ligação ao WiFi e os sensores corretamente ligados, vamos começar pelas funções básicas que se encontram na ferramenta “ArduBlocks”.

Para isso, primeiro devemos ligar, com ajuda de um cabo USB, desde o teu computador para a placa ESP32 (referida na Figura 32) e abrimos o Arduíno IDE e neste software a ferramenta ArduBlocks (referida na Figura 29).

Na figura 49 vê-se a página principal de ArduBlocks, na parte esquerda encontram-se o resto de blocos úteis para o funcionamento do nosso robô.


Figura 50 - ArduBlocks aberto

3.1.Piscar LED e ligar WiFi

Na parte esquerda, vamos começar por blocos de nível iniciante e vamos clicar em “Beginner RBC_IPL” e movimentamos o bloco “Flashing Led” que fará piscar um LED da placa ESP32, no bloco “Robô OTA”, que é o bloco que usaremos nas tarefas de nível iniciante, existem dois blocos na parte “ssid” e “password” onde em ssid colocaremos o nome da rede WiFi à que pretendemos ligar o robô, e em password escrevemos a palavra-passe daquela rede WiFi, quando estiver prontos os blocos ligados como na Figura 51, clicamos em “Upload to Arduíno”, isto faz que sejam transformados os blocos em linguagem de programação “C++”, automaticamente será enviado o código para a placa ESP32 e em instantes piscará o LED e isto garante a ligação ao WiFi. Se der erro ao carregar o programa, temos de pressionar o botão “BOOT” do ESP32 enquanto carregamos o programa.


Figura 51 - Upload to Arduíno

3.2.Apagar Bloco.

Para apagar um bloco qualquer da ferramenta “ArduBlocks” basta movimentar o bloco que queremos apagar para a parte esquerda como é mostrado na Figura 52. Neste exemplo apagamos todos os blocos que anteriormente colocámos.

Figura 52 - Apagar blocos

3.3.Fazer Círculos.

Agora testaremos os movimentos do robô, para verificar se não existe problemas de ligação na montagem do robô, primeiro utilizaremos o bloco chamado “Go in Circles” que movimentará o robô em círculos fazendo que uma roda vaia para um sentido e a outra roda para o sentido oposto, para isto basta colocar os blocos na ordem mostrada na Figura 53. clicamos em Upload to Arduíno e o código será carregado para o Arduíno IDE.

Figura 53 - Go in Circles

3.4.Movimentos aleatórios.

Para experimentar mais movimentos do que mover em círculos, vamos fazer a próxima sequência de blocos na ferramenta “ArduBlocks”, a usar o bloco chamado “Walking Randomly” que faz que o robô percorra movimentos aleatórios, carregamos em “Upload to Arduíno” e o robô fará a tarefa, como na Figura 54.


Figura 54 - Walking Randomly

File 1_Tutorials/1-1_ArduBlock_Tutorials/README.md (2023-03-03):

# Tutoriais para Ardublock

Os presentes tutoriais deverão facilitar a compreensão da linguagem de programação por blocos.

Pode encontrar as atividades associadas em [/2_Atividades/2-1_Atividades_para_ArduBlock/](https://github.com/Guilherme010101/iModBot2/tree/master/2_Activities/2-1_ArduBlock_Activities).

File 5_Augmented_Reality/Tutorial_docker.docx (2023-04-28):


iModBot


# Docker

## Guia para iniciantes


Elaborado por:

Nelson Henriques – 2190514

Orientado por: Carlos Neves Luís Conde

# Índice

# 1. Introdução

O Docker é uma ferramenta utilizada para tornar mais fácil criar, implementar e executar aplicações utilizando containers. Os containers permitem que o desenvolvedor empacote a aplicação bem como todas as partes de que precisa, como bibliotecas e outras dependências, e implemente-o como um package. Assim o desenvolvedor pode ter certeza de que a aplicação será executada em qualquer outra máquina Linux, independentemente de quaisquer configurações personalizadas que a máquina possa ter, que podem ser diferentes da máquina usada para escrever e testar o código.

De certa forma, o Docker é idêntico a uma máquina virtual. Mas, ao contrário de uma máquina virtual, em vez de criar um sistema operativo virtual completo, o Docker permite que as aplicações usem o mesmo kernel Linux do sistema em que estão a ser executadas, requer apenas que as aplicações sejam enviadas com coisas que ainda não estão a ser executadas no host. Isto possibilita um aumento significativo no desempenho e reduz o tamanho da aplicação.

Compose é uma ferramenta utilizada para definir e executar aplicações Docker compostas por vários containers. O Compose utiliza arquivos YAML para configurar os serviços da aplicação. Então, com um único comando cria e inicia todos os serviços da configuração.

## 1.1. Objetivos

Pretende-se com este tutorial fornecer os conhecimentos básicos para a utilização do

software Docker e Docker-Compose.

Ao longo do tutorial vai-se abordar os seguintes temas:

- Terminologia Docker;
- Instalar o software Docker e Docker-Compose;
- Comandos básicos Docker.
- Comandos básicos Docker-Compose.

(Este tutorial é destinado ao Docker e Docker-Compose em um sistema Linux 20.04)

2. Terminologia Docker

## 2.1. Images

As images do docker são a "receita" para um container. As images contém todas as definições de como inicializar o ambiente Linux. Normalmente, uma imagem Docker existe para cumprir especificamente uma tarefa. Por exemplo, uma imagem definiria o seu servidor web e outra imagem definiria a database subjacente.

## 2.2. Containers

Os containers são instanciações de imagens. Eles são uma forma de imagem. Compare-a com a programação orientada a objetos, então sua classe seria uma imagem e uma instância da classe, um container. Outra comparação seria com contentores reais num cargueiro. Estes tem uma aparência idêntica por fora, mas por dentro são/podem ser completamente diferentes. Alguns factos interessantes sobre containers:

    - Os containers não são persistentes. Assim que não estiverem a ser utilizados eles são desligados, ou até mesmo eliminados.
    - Um container só vive enquanto um processo é executado dentro dele.
    - Os containers podem incluir dados, mas estes também não são persistentes. Se quiser torná-los persistentes, pode-se utilizar volumes.
    - Para comunicar entre containers, usa-se os mesmos protocolos que se usariam para comunicar entre computadores (por exemplo, TCP / IP).

## 2.3. Volumes

Os volumes podem ser usados como camada de dados subjacente. Estes podem ser utilizados por vários containers. Todos os dados guardados num volume podem ser acedidos por qualquer container conectado a ele.

## 2.4. Networks

O Docker vem com as suas próprias capacidades de networking. O nome de um container é seu nome de host. A maneira mais fácil de experimentar isso é ter dois containers em execução e executar o comando para verificar o ping em um container de dentro de outro container. O Docker Compose irá gerar sua própria sub-rede.

# 3. Instalar o software Docker e Docker-Compose

## 3.1. Docker

Iremos instalar utilizando o repositório oficial do Docker.

1. Atualize as packages do apt e adicione novas para o mesmo poder utilizar o repositório por HTTPS:

sudo apt-get install \ apt-transport-https \ ca-certificates \ curl \

gnupg \

lsb-release

sudo apt-get update

2. Adicione a chave GPG do Docker.

curl -fsSL https://download.docker.com/linux/ubuntu/gpg | sudo gpg --dearmor

-o /usr/share/keyrings/docker-archive-keyring.gpg

3. Usa o seguinte comando para criar o repositório local.

echo \

"deb [arch=amd64 signed-by=/usr/share/keyrings/docker-archive-keyring.gpg] https://download.docker.com/linux/ubuntu \

$(lsb_release -cs) stable" | sudo tee /etc/apt/sources.list.d/docker.list >

/dev/null

4. Instale o Docker.

sudo apt-get install docker-ce docker-ce-cli containerd.io

sudo apt-get update

5. Verifique se o Docker foi instalado corretamente..

docker --version

deverá obter algo semelhante á Figura 1

Figura 1 - Versão do Docker.

## 3.2. Docker-Compose

1. Descarregue a versão mais recente e estável do Docker-Compose

sudo curl -L "https://github.com/docker/compose/releases/download/1.29.1/docker-compose-

$(uname -s)-$(uname -m)" -o /usr/local/bin/docker-compose

2. Dê permissão de execução ao binário descarregado.

sudo chmod +x /usr/local/bin/docker-compose

3. Verifique se o Docker-Compose foi instalado corretamente.

docker-compose --version

Deverá obter algo semelhante á Figura 1

Figura 2 - Versão do Docker-Compose.

# 4. Comandos básicos Docker

  1. Iremos começar correndo o clássico “Hello World”.

docker run hello-world

Deverás obter a seguinte resposta (Figura 3).


Figura 3 - Output de "Hello World"

A output já descreve muito bem o que acontece ao executar este comando.

Iniciou-se um container, cujo a imagem foi descarregada do Docker hub, de seguida executou-o e enviou a resposta para o terminal.

Se der erro e aparecer algo parecido como a Figura 4 basta dar permissão ao ficheiro docker.sock, utilizando o comando abaixo.

sudo chmod 666 /var/run/docker.sock

Figura 4 – erro ao executar o docker

  2. Vê todos os containers que estão em execução ou foram executados.


docker ps -a

Figura 5 - containers que estão em execução ou foram executados

Os “Names” são gerados aleatoriamente, podemos referir-nos aos containers pelos “Names” ou pelo “container id” (Figura 5)

  3. Execute novamente o “Hello World” mas desta vez iremos atribuir um nome, assim não dependemos de um nome gerado aleatoriamente.

docker run --name My-HW hello-world

  4. Execute novamente o comando do passo nº2 e verifique que o nome é igual ao que foi atribuído no comando anterior (Figura 6).


Figura 6 - container com o nome customizado

  5. Agora vamos executar um container que contem o ubunto (como este container não está localmente o Docker ira descarregá-lo do Docker Hub) e ao mesmo tempo iremos atribuir um nome customizado.


docker run -it --name my-linux-container ubuntu bash

Figura 7 - ubunto container

Agora está dentro do container ubunto (Figura 7) onde pode executar qualquer comando Linux isto é bastante útil quando estamos num sistema windows ou macOS, para sair basta escrever “exit”.

  6. Mais uma vez ao executar o comando do passo nº2 para ver o estado de todos os containers executados ou em execução até ao momento (Figura 8).


Figura 8 - Containers executados ou em execução

  7. Verifique quais as imagens que tem guardados localmente.


docker images

Figura 9 - docker images

Este comando pode ser bastante útil pois permite saber todas as informações principais das “images” (Figura 9), como estão guardados localmente a sua execução da próxima vez será instantânea.

  8. Uma vez iniciado um container com um nome pré-definido pelo utilizador o mesmo já não pode ser iniciado com o mesmo nome, por isso podemos executar o seguinte comando de modo a limpar o “histórico” de containers executados (Figura 10).


docker rm $(docker ps -a -f status=exited -q)

Figura 10 – output

  9. Verifique que a lista está limpa correndo o comando do passo nº2.
  10. Inicie um container e ao mesmo tempo conecte-o a uma pasta local, para isso crie uma pasta no seu sistema operativo local e guarde o seu caminho, substituindo-o no comando abaixo.

docker run -it --name my-linux-container --rm -v [diretoria local] ubuntu bash

- -it (interactive container) – entra no mesmo assim que inicia.
- --rm – assim que termina elimina-o da lista.
- -v – comando para conectar a diretoria local sendo que a pasta a partilhar tem que anteceder “:”. Ex:

docker run -it --name my-linux-container --rm -v

/home/ipleiria/Desktop:/meus_dados ubuntu bash

  11. Verifique que a pasta foi partilhada executando o comando ls dentro do container.


Figura 11 - pasta partilhada

Como pode observar a pasta foi partilhada corretamente (Figura 11).

  12. Execute um comando no container ubuntu, para isso, abra um novo terminal (não feche o atual), e utilize o seguinte código.

docker exec -it my-linux-container echo "Hello World"

Com este código irá imprimir um Hello World (Figura 12), sendo que depois do nome do

container vem o comando a executar no mesmo.


Figura 12 - comando executado

  13. Crie um Docker image, para isso crie uma nova pasta e atribua-lhe o nome “My-Docker- Image”, dentro dessa pasta crie um ficheiro com o nome “Dockerfile” (certifique-se que não tem um tipo de ficheiro ex: .txt), abra-o com um editor de texto, neste momento deverá ter algo semelhante á Figura 13.


Figura 13 - ficheiro Dockerfile

  14. No ficheiro escreva as seguintes linhas de código (Figura 14), guarda e fecha o ficheiro.


Figura 14 - código a escrever

Existe uma grande variedade de “Keywords” para criar imagens Docker estas podem ser encontradas aqui: https://docs.docker.com/engine/reference/builder/.

  15. No terminal vá á diretoria criada (esta diretoria varia dependendo de onde criou a pasta).

cd /home/ipleiria/Desktop/My-Docker-Image

  16. Construa a imagem.

doc

- -t – atribui um nome á imagem.

Deverá obter algo semelhante à Figura 15.


Figura 15 - imagem criada

  17. Verifique que a imagem foi criada (Figura 16).


docker images

Figura 16 - lista de imagens locais

  18. Corra a imagem criada.


docker run my-ubuntu-image

Figura 17 - output do meu container

Como pode observar ao executar o container ele escreveu no terminal o que foi escrito no Dockerfile (Figura 17).

Ex:

Pretende iniciar um ubuntu Docker já com o python3 instalado, para isso no ficheiro criado anteriormente basta trocar o “CMD echo "Hello World - From My Container"” por “RUN apt-get upgrade && apt-get update && apt-get install -y python3” e contruir novamente a imagem, assim terá uma imagem ubunto com o python3 já instalado.

Pode também guardar o estado do seu container em uma nova imagem através do seguinte comando:

docker commit $CONTAINER_ID image name

# 5. Comandos básicos Docker-Compose

  1. Descarregue o conteúdo do repositório, este será o exemplo utilizado para o tutorial. (https://github.com/jakewright/tutorials/tree/master/docker/02-docker-compose)

Nessa pasta irás encontrar 4 ficheiros, “product”, “Website”, “readme.md” e “Docker- compose.yml”, o ficheiro “Docker-compose.yml” é o ficheiro onde estão todas as definições da aplicação, que neste caso é um web site muito simples.

Este exemplo está pronto a ser executado, mas antes disso iremos entender o que irá o ficheiro “Docker-compose.yml” fazer.

  2. Abra o ficheiro “Docker-compose.yml” com o seu editor preferido (Figura 18).


Figura 18- Docker-Compose.yml

Version: – Versão em que está a ser escrita o ficheiro (opcional a partir da versão 1.27). services: – serviços a iniciar.

Product-service e website – nome dos serviços.

O restante são as dependências e definições dos serviços sendo que tem de ser adaptadas ao que pretende realizar, para mais informação consulte este link: https://docs.docker.com/compose/compose-file/

  3. Abra o terminal e vá até á diretoria descarregada.

cd /home/ipleiria/Desktop/02-docker-compose/

  4. Agora irá “construir” a aplicação com base no ficheiro criado (Figura 19).


docker-compose build

Figura 19 - construção terminada

  5. Agora irá iniciar a aplicação criada (Figura 20).


docker-compose up

Figura 20 - aplicação iniciada

  6. Aceda a localhost:5000 no seu browser, deverá aparecer algo semelhante á Figura 21.


Figura 21 - website exemplo

Caso dê um erro semelhante ao da Figura 22, corra o seguinte comando:

sudo chmod 755 website


Figura 22 - possível erro

Docker Guia para iniciantes

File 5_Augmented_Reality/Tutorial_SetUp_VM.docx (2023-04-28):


iModBot


# SetUp Virtual Machine

xubuntu


Elaborado por:

Nelson Henriques – 2190514

Orientado por: Carlos Neves Luís Conde

Índice

# 1. Introdução

VirtualBox é um software de virtualização desenvolvido pela empresa Innotek e comprado pela empresa Oracle que, como o VMware Workstation, visa criar ambientes para instalação de sistemas distintos. Este permite a instalação e utilização de um ou mais sistemas operacionais dentro de outro, assim como seus respetivos softwares, como dois ou mais computadores independentes, mas partilham fisicamente o mesmo hardware.

## 1.1. Objetivos

Pretende-se com este tutorial guiar qualquer pessoa na criação de uma Virtual Machine dedicada ao ROS2 utilizando o software VirtualBOX. Ao longo do tutorial vai-se abordar os seguintes temas:

- Criar uma VM (xubuntu-20.04);
- Configurações;
- Instalar GuestAdditions.

(Este tutorial pressupõe que já tem instalado o VirtualBox, todos os comandos utilizados têm como utilizador ipleiria, tendo que ser substituído pelo seu nome de utilizador, download do xubuntu-20.04 – http://mirror.us.leaseweb.net/ubuntu-cdimage/xubuntu/releases/22.04/release/

# 2. Criar uma VM


1. Abra o virtual box e clique em New (Figura 1).

Figura 1 - New virtual machine

2. Dá um nome á tua maquina virtual, escolhe o local onde será isntalada e seleciona o tipo de sistema operativo e a arquitetura (32 ou 64 bits) (Figura 2).


Figura 2 - Seleção do nome e sistema operativo

3. Selecione a quantidade de Ram para dedicar á maquina virtual cerca de 1/3 da memoria do seu computador (Figura 3).


Figura 3 – Ram dedicada

4. Crie um novo disco virtual (Figura 4).


Figura 4 - Criar um disco virtual

5. Selecione VDI (Figura 5)


Figura 5 - VDI

6. Selecione “Dynamically allocated” assim o disco virtual irá aumentar de tamanho consoante a sua utilização (Figura 6).


Figura 6 - Dynamically allocated

7. Escolha a capacidade do disco, é preferível escolher um valor grande pois o disco virtual só irá ocupar o espaço que necessita (Figura 7), e faça “Create”.


Figura 7 - Tamanho do disco virtual

8. Selecione a maquina virtual criada e vá a “Settings” (Figura 8).


Figura 8 - Máquina criada

9. Vá a “Storage” e selecione o disco “Empty” e selecione o ficheiro .iso (Figura 9).


Figura 9 - Definições de Storage

10. Em “Network” mude “Attached to:” para “Bridge adapter” e de seguida selecione o seu adaptador (Figura 10).


Figura 10 – Definições de Network

2.1.Instalar Guest Additions

1. Vá a “Devices” e clique em “Insert Guest Additions CD image” (Figura 11).


Figura 11 – Inserir o disco virtual Guest Additions

2. Agora corra os seguintes comandos no terminal (a versão poderá ter que ser alterada)(Figura 12).


sudo ./autorun.sh

cd /media/ipleiria/VBox_GAs_6.1.20/

Figura 12 – Instalando as Guest Additions

3. Ao terminar a instalação reinicie a máquina virtual.

A instalação está concluída.

Set Up Virtual Machine xubuntu

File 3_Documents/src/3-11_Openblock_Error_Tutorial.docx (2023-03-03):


iModBot

# Tutorial

Erro na Instalação do Openblocks

Elaborado por:

Abel Teixeira – 2180522 Samuel Lourenço – 2180356

Verificado por:

Marco Pereira – 2190516 Nelson Henriques – 2190514

Orientado por: Carlos Neves Luís Conde

ÍNDICE

# INTRODUÇÃO

Pode acontecer que no momento de executar o seguinte comando “mvn install”, para instalar o Openblocks no projeto Ardublock, que lhe surja um erro semelhante ao da Figura 1, que indica que a versão do java não é suportada.

Neste momento já deve ter executado todos os passos do tutorial “Editar_Ardublock_com_Eclipse”, até ao passo 5.6 (inclusive).


Figura 1 - Erro ao executar o comando “mvn install”

## 1. Abrir o ficheiro “pom”

Na pasta “Ardublock-Workspace”, entrar na pasta “openblocks-master” e abrir o ficheiro “pom” com o Bloco de notas ou Notepad++ (Figura 2).


Figura 2 – Abrir o ficheiro “pom”

## 2. Localizar a versão


Procure por as linhas de texto “<source> 1.6 </source>” e “<target> 1.6 </target>”, geralmente localizadas nas linhas 24 e 25 (Figura 3).

Figura 3 – Localizar a versão


## 3. Alterar os valores

Após localizar os valores, deve de alterá-los de “1.6” para “1.8”, ficando com o aspeto da Figura

  4. De seguida pode guardar o ficheiro e fechá-lo.

Figura 4 – Alterar os valores

## 4. Instalar o Openblocks

Neste momento, pode voltar a instalar o Openblocks no projeto Ardublock, executando o comando “mvn install” na PowerShell. Deverá ser instalado com sucesso aparecendo uma mensagem idêntica à da Figura 5.


Figura 5 – Instalar o Openblocks

Tutorial Erro na Instalação do Openblocks

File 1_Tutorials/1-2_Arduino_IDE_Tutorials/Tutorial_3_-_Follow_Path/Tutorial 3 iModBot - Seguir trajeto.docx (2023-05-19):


| Tutorial – Movimento iModBot@ipleiria.pt

# Introdução

O robô iModBot é um veículo elétrico de pequenas proporções controlado pelo microcontrolador ESP32. Este microcontrolador pode ser programado usando a linguagem C/C++ e o software gratuito Arduino IDE.

Este tutorial vai focar-se na função de seguir automaticamente um trajeto.

Para efetuar a tarefa de seguir um trajeto autonomamente é necessário verificar constantemente se há algum obstáculo a obstruir o caminho, caso haja é necessário parar os motores.

De seguida é necessário verificar os sensores infravermelho de modo a determinar o percurso que o robô deve seguir.

Embora pareca um processo simples há varias coisas a ter em conta.

O seguinte fluxograma descreve os procedimentos para executar a tarefa de seguir um trajeto (linha) autónomamente.


Seguir trajeto – exemplo 1

Exemplo:

#include <iModBot.h>

iModBot robot; // Criar um objeto chamado "robot"

void setup()

{

robot.begin(); // Configura os pinos.

robot.beginAutoDrive(); // Inicia a função de condução autónoma.

}

void loop()

{

int info = 0; // Variável para guardar o numero devolvido pela função autoDrive().

int command = 0; // variável para lembrar que comandos já foram executados.

info = robot.autoDrive(0); // Aqui copiamos o valor devolvido pela função para a variável info.

/* Sempre que usarem a função autoDrive() têm de enviar um valor, estes são as instruções aceites:

0 -> Enviar 0 ou qualquer outro número (até 255) não listado se não quiser dar instruções ao robô.

1 -> Enviar 1 para colocar o robô a rodar para a direita até encontrar uma linha.

2 -> Enviar 2 para colocar o robô a rodar para a esquerda até encontrar uma linha.

3 -> Enviar 3 para dizer ao robô para seguir em frente.

4 -> Enviar 4 para dizer ao robô para recuar, tenha em atenção que o robô pode-se desalinhar

ligeiramente devido à roda traseira.

*/

}

#### Descrição

A biblioteca “RobotOnLine_Rev2” dispõe de funções que permitem facilmente implementar a tarefa de seguir um trajeto de forma autónoma.

#### Sintaxe

beginAutoDrive(); // Inicia a função de condução autónoma.

autoDrive(byte ); // Realiza tarefas necessárias para a condução autónoma.

#### Parâmetros

autoDrive(numero )

a variável número pode ter os seguintes valores:

0 sem efeito.

1 robô roda para a direita até encontrar uma linha.

2 robô a rodar para a esquerda até encontrar uma linha.

3 robô segue em frente.

4 robô recua.

A função autoDrive(byte) pode devolver um dos seguintes valores:

1 multiplas linhas encontradas.

2 obstaculo encontrado.

3 não foram encontradas linhas.

#### Respostas

Nenhum

Seguir trajeto – exemplo 2

Exemplo:

#include <iModBot.h>

iModBot robot;

void setup()

{

Serial.begin(115200);

robot.begin();

}

void loop()

{

if((robot.readS1() == 1) && (robot.readS2() == 1) && (robot.readS3() == 0) && robot.readS1() == 1) &&

(robot.readS2() == 1))

{

robot.forward(110);

while((robot.readS1() == 1) && (robot.readS2() == 1) && (robot.readS3() == 0) && robot.readS1() == 1) &&

(robot.readS2() == 1))

{

;

}

}

else if((robot.readS1() == 1) && (robot.readS2() == 0) && (robot.readS3() == 1) && robot.readS1() == 1) &&

(robot.readS2() == 1))

{

robot.rotateLeft(110);

while((robot.readS1() == 1) && (robot.readS2() == 0) && (robot.readS3() == 1) && robot.readS1() == 1) &&

(robot.readS2() == 1))

{

;

}

}

else if((robot.readS1() == 0) && (robot.readS2() == 1) && (robot.readS3() == 1) && robot.readS1() == 1) &&

(robot.readS2() == 1))

{

robot.rotateLeft(110);

while((robot.readS1() == 0) && (robot.readS2() == 1) && (robot.readS3() == 1) && robot.readS1() == 1) &&

(robot.readS2() == 1))

{

;

}

}

else if((robot.readS1() == 1) && (robot.readS2() == 1) && (robot.readS3() == 1) && robot.readS1() == 0) &&

(robot.readS2() == 1))

{

robot.rotateRight(110);

while((robot.readS1() == 1) && (robot.readS2() == 1) && (robot.readS3() == 1) && robot.readS1() == 0) &&

(robot.readS2() == 1))

{

;

}

}

else if((robot.readS1() == 1) && (robot.readS2() == 1) && (robot.readS3() == 1) && robot.readS1() == 1) &&

(robot.readS2() == 0))

{

robot.rotateRight(110);

while((robot.readS1() == 1) && (robot.readS2() == 1) && (robot.readS3() == 1) && robot.readS1() == 1) &&

(robot.readS2() == 0))

{

;

}

}

else if((robot.readS1() == 1) && (robot.readS2() == 0) && (robot.readS3() == 0) && robot.readS1() == 1) &&

(robot.readS2() == 1))

{

robot.rotateLeft(110);

while((robot.readS1() == 1) && (robot.readS2() == 0) && (robot.readS3() == 0) && robot.readS1() == 1) &&

(robot.readS2() == 1))

{

;

}

}

else if((robot.readS1() == 1) && (robot.readS2() == 1) && (robot.readS3() == 0) && robot.readS1() == 0) &&

(robot.readS2() == 1))

{

robot.rotateRight(110);

while((robot.readS1() == 1) && (robot.readS2() == 1) && (robot.readS3() == 0) && robot.readS1() == 0) &&

(robot.readS2() == 1))

{

;

}

}

else if((robot.readS1() == 1) && (robot.readS2() == 1) && (robot.readS3() == 0) && robot.readS1() == 0) &&

(robot.readS2() == 0))

{

robot.rotateRight(110);

while((robot.readS1() == 1) && (robot.readS2() == 1) && (robot.readS3() == 0) && robot.readS1() == 0) &&

(robot.readS2() == 0))

{

;

}

}

else if((robot.readS1() == 0) && (robot.readS2() == 0) && (robot.readS3() == 0) && robot.readS1() == 1) &&

(robot.readS2() == 1))

{

robot.rotateLeft(110);

while((robot.readS1() == 0) && (robot.readS2() == 0) && (robot.readS3() == 0) && robot.readS1() == 1) &&

(robot.readS2() == 1))

{

;

}

}

else if(((robot.readS1() == 0) && (robot.readS2() == 0) && (robot.readS3() == 0) && robot.readS1() == 0) &&

(robot.readS2() == 0)) || (robot.readCLP() == 1) ||

(robot.distance() <= 10))

{

robot.stopMotors();

}

}

#### Descrição

Este exemplo permite ao robô seguir um trajeto sem recorrer à função de condução autónoma disponibilizada pela biblioteca “RobotOnLine_Rev2”

Note que há ciclos while() após cada instrução que afeta o movimento do robô, isto serve para impedir que a instrução seja repetida indefinidamente.

#### Sintaxe

Parâmetros

state = variável que recebe o valor da função, 1 ou 0, consoante o estado do pino.

#### Respostas

Nenhum

Tutorial – Movimento iModBot@ipleiria.pt Página 30 de 30

Politécnico de Leiria 2019/2020

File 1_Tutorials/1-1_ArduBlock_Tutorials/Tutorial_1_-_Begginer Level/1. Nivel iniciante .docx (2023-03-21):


| Instituto de Engenharia de Sistemas e Computadores (INESC) de Coimbra Tutorial – Nível Iniciante

Programar o robô iModBot (https://github.com/Guilherme010101/iModBot2)

por blocos


Alunos: Abel Teixeira - 2180522

Samuel Lourenço - 2180356

Docente: Carlos Neves

Luís Conde

Ano letivo: 2019/2020

# Abrir o ArduBlock

Se já tens o ArduBlock aberto pode saltar este passo e passar para o Nível Iniciante.

Caso ainda não tenha, comece por abrir o Arduíno IDE.


No Arduíno IDE clique “Tools” → “ArduBlock” e já tem ao ArduBlock aberto pronto para construir o programa.


# Guia básico do ArduBlock

Este guia é para ensinar o funcionamento básico do ArduBlock para o utilizador saber como utilizar e o nome de cada ferramenta.

O botão “Upload to Arduíno” converte o programa de blocos para linguagem C++ no Arduíno IDE.

O botão “Open” abre o programa que guardaram.

Os botões “Save” e “Save as” guardam o vosso programa onde o colocarem.

No botão “New” abre um novo ArduBlock.

O botão “Serial Monitor” abre uma janela onde mostra os valores que nós enviamos para lá.

O botão “Go to Web Site” reencaminha-te para o site do ArduBlock, este link: http://blog.ardublock.com/ .

O botão “Save as image…” tira uma foto ao teu programa e guarda-a onde indicar.

Nesta coluna mostra as várias abas, e ao clicar nelas mostra os blocos que tem dentro de cada uma.

Nós vamos começar por utilizar as 4 últimas abas.

Este retângulo mostra o espaço livre que tem para fazer o programa.

Para eliminar algum bloco que não queiram basta arrastá-lo para cima da coluna das abas e largar, ele é eliminado do espaço de trabalho como pode ver na figura abaixo.


# Nível Iniciante (Beginner)

Neste nível basta só colocar um bloco no loop do bloco “Basic OTA”.

Caso não esteja ligado ao ESP32 com o cabo micro USB e queira ligar através do wifi tem de clicar no bloco branco “ssid” e colocar o nome da internet e no bloco “password” colocar a passe da internet. Fica a comunicar com o ESP32 sem fios, sem se esquecer da alimentação dele.

## 1. Bloco “Fashing Led”

Neste primeiro bloco verde vai fazer piscar o led azul que está ligado no pino 2. O objetivo é fazer piscar o led para saber se o ESP32 está a comunicar por wifi. Para isso tem de abrir a aba verde com o nome “Beginner level” e arrastar o bloco “Fashing Led” para dentro do loop do bloco “Basic OTA”, como pode ver na figura abaixo.


Não se esqueça de colocar o “ssid” e a “password”. Depois clique no botão “Upload to Arduíno” que vai converter o programa que fizemos para a linguagem C++ no Arduíno IDE e envia-o para o ESP32 que vais fazer piscar o led.

## 2. Bloco “Go in circles”

No segundo bloco verde o robô vai andar à roda. O objetivo é saber se as rodas estão bem ligadas. Para isso basta só colocar o bloco “Go in circles” no loop retirando o bloco anterior.


## 3. Bloco “Walking Randomly”

No terceiro bloco verde o robô vai andar aleatoriamente. O objetivo é saber se está tudo bem ligado e as ordens do ESP32 (avançar, recuar, esquerda, direita e parar) estão a ser recebidas. Para isso basta só colocar o bloco “Walking Randomly” no loop retirando o bloco anterior.


## 4. Bloco “Guide by Bluetooth”

No quarto bloco verde tem de tirar o bloco “Robo OTA” substituindo-o pelo bloco “Guide by Bluetooth” e definir a velocidade de 0 a 255, como pode ver na figura abaixo.


Depois de ter enviado o programa para o ESP32, vai à “Play Store” do telémovel e procure por “Ultimate Bluetooth Joystick” e instale. Se não conseguir encontrar a app na “Play Store” é porque o seu telemóvel tem uma versão Android mais moderna e por isso a loja emite a aplicação. Felizmente é possível instalar a aplicação independente da sua versão Android através de um apk, que está neste link:

https://m.apkpure.com/ultimate-bluetooth-joystick/com.cavalcante_fgc.joystick/download.

Depois de instalar o apk basta ir à secção de transferências do google e selecionar o apk, instalando assim a app. Já com a aplicação instalada abra e clique no icon no canto superior direiro parecido com uma roda dentada e clique em “Ajustar os botões”.


Clique nas setas pretendidas como mostra a figura em baixo e altere onde diz “Pressionado” e coloca a letra consoante a seta, onde diz “Solto” retira a letra e não coloca nada.

Nota: as letras tens de ser em minúsculas.

“a” – Avançar;

“b” – Virar à direita;

“c” – Virar à esquerda;

“d” – Recuar;

“e” até “z” – Para o robô.


Já com as alterações feitas clica “Parar a configuração”, e depois no “CONECTAR” vai abrir uma nova janela e pressiona em “Procurar”, escolhe o ESP32 e estás pronto para controlar o robô por Bluetooth.


## 5. Bloco “Follow Line”

No quinto bloco verde o robô vai seguir a linha preta e basta só colocar o bloco no loop e colocar o robô em cima da linha e ele vai seguir.


Nível Iniciante – iModBot@ipleiria.pt Página 30 de 30

Politécnico de Leiria 2019/2020

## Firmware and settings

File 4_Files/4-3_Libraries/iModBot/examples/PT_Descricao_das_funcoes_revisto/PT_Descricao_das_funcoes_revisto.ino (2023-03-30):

/*  Neste exemplo serão exemplificadas maioria das funções da biblioteca RobotOnLine.
    As funções relacionadas com a funcionalidade de condução automática não serão descritas neste exemplo.
*/

#include <iModBot.h>  // É necessário incluir a biblioteca

iModBot robot;  // É sempre necessário criar esta linha, a palavra "robot" pode ser outra
//qualquer (desde que não faça interferência com a linguagem arduino).



void setup()
{
  /*  A função " editWheelPin(uint8_t , uint8_t ); " permite alterar os pinos onde são ligados os sensores òpticos.
      Se esta função for usada, a mesma deve ser chamada antes da função begin();
  */
  //  ( pino do encoder da roda esquerda, pino do encoder da roda direita)
  robot.editWheelPin(26 , 27);  // Estes são os pinos que a biblioteca usa por defeito.

  //  - - - - - - - - - - - - -

  /*  A função " editMotorPin(uint8_t , uint8_t , uint8_t , uint8_t ); " pode ser chamada depois da função begin(); mas não é aconselhado.
      Permite alterar onde são ligadas as conecções para controlar os motores.
      Na altura em que este exemplo foi criado foi usada uma placa com o CI L293D, e os nomes dos pinos da mesma eram IN1, IN2, IN3, IN4.
  */
  //                (IN1,IN2,IN3, IN4)
  robot.editMotorPin( 4 , 16 , 17, 18 ); // Estes são os pinos que a biblioteca usa por defeito.

  //  - - - - - - - - - - - - -

  /*  A função " editUltrasonicPin(uint8_t , uint8_t ); " pode ser chamada depois da função begin(); mas não é aconselhado.
      Esta função permite alterar os pinos que conectam  ao sensor ultrassónico HC-SR04.
  */
  //                 (trig pin, echo pin );
  robot.editUltrasonicPin(  12, 14);  // Estes são os pinos que a biblioteca usa por defeito.

  //  - - - - - - - - - - - - -

  /*  A função " editSensorPin(uint8_t , uint8_t , uint8_t , uint8_t , uint8_t , uint8_t , uint8_t ); "
      pode ser chamada depois da função begin(); mas não é aconselhado.
      Permite alterar os pinos onde são estabelecidas as ligações à placa frontal que possui vários sensores de infravermelho.
      Na altura em que este exemplo foi escrito estava a ser usada uma placa com o CI 74HC14,
      e os pinos S1, S2, S3, S4, S5, CLP, Near.
  */
  //                 (  S1, S2, S3, S4, S5,CLP,Near)
  robot.editSensorPin(  25, 33, 32, 35, 34, 39, 36);  // Estes são os pinos que a biblioteca usa por defeito.

  //  - - - - - - - - - - - - -

  /*  A unção " begin(); " irá configurar todos os pinos e interrupções em uso pela biblioteca.
      Os canais de PWM 0,1,2,3 do ESP32 serão usados pela biblioteca com uma resolução de 8 bit (0 to 255).
  */
  robot.begin();  // Esta função é essencial.

  //  - - - - - - - - - - - - -

  /*  A função "setSpeeds(byte, byte, byte)" permite dizer ao robô qual o dutty cycle
      que deverá corresponder às velocidades máxima, média e mínima.
  */
  robot.setSpeeds(255, 200, 180);

  //  - - - - - - - - - - - - -

  Serial.begin(115200);
}

void loop()
{
  byte dist = robot.distance(); // Esta função devolve a distância (em cm) medida pelo sensor HC-SR04, O valor devolvido varia de 0 to 255 cm
  Serial.print("A distância medida é de: ");
  Serial.print(dist);
  Serial.println("cm");

  //  - - - - - - - - - - - - -

  /*  As funções "turnLeft(uint16_t);" e "turnRight(uint16_t);" permitem dizer ao robô para rodar x graus
      para a direita ou esquerda (dependendo de qual das funções é chamada).
      Se for enviado um 0 o robô irá tentar rodar 90 graus. Se for enviado um valor acima de 360 o robô irá apenas rodar 360 graus.

  */
  robot.turnLeft(0);
  robot.turnRight(0);

  //  - - - - - - - - - - - - -

  /*  As funções "steerLeft(byte );" e "steerRight(byte );" permitem dizer ao robô para virar para a 
      direita ou esquerda (dependendo de qual das funções é chamada).
      Cada uma destas funções irá fazer o robô virar ao reduzir a velocidade da roda.
  */
  robot.steerLeft(255);   // Deves especificar a velocidade máxima (1 a 255) à qual o robô deve circular.
  robot.steerRight(255);

  //  - - - - - - - - - - - - -

  /*  As funções " rotateLeft(byte ); " e " rotateRight(byte ); " permitem dizer ao robô para começar a rodar 
      para a direita ou esquerda (dependendo de qual das funções é chamada) a x velocidade. 
      A velocidade especificada (de 0 a 255) irá indicar a velocidade à qual o robô deverá rodar.
      O robô continuará a rodar até que receba novas instruções.
  */
  robot.rotateLeft(255);  //  Introduzir um valor de 1 to 255, ciclos de trabalho baixos (numeros baixos) poderão não ser suficientes para o
  robot.rotateRight(150); //  robô conseguir virar. Um 0 não fará o robô rodar.

  //  - - - - - - - - - - - - -

  /*  A função "stopMotors();" para ambos os motores.
  */
  robot.stopMotors();

  //  - - - - - - - - - - - - -

  /*  A função "forward(byte );" permite dizer ao robô para avançar a x velocidade.
      Pode ser enviado um valor de 1 a 255, um 0 fará os motores pararem.
  */
  robot.forward(255);

  //  - - - - - - - - - - - - -

  /*  A função "reverse(byte );" permite dizer ao robô para recuar a x velocidade.
      Pode ser enviado um valor de 1 a 255, um 0 fará os motores pararem.
  */
  robot.reverse(255);

  //  - - - - - - - - - - - - -

  /*  As funções "leftWheel(short );" e "rightWheel(short );" permitem controlar a roda direita e/ou esquerda individualmente.
      Um valor negativo faz a rodar andar para trás, um valor positivo faz a mesma andar para a frente.
      Pode ser enviado um valor de -255 a 255, um 0 fará o motor parar.
  */
  robot.leftWheel(-255);
  robot.rightWheel(-255);

  //  - - - - - - - - - - - - -

  /*  As funções "getLeftEncoderCount();" e "getRightEncoderCount();" devolvem o numero de pulsos contados pelo encoder direito e/ou esquerdo.
      Estas funções devolvem um número de dois bytes do tipo short. 
  */
  short leftEncoder = robot.getLeftEncoderCount();
  short rightEncoder = robot.getRightEncoderCount();

  /*  A função "clearEncoderCount();" coloca o número de pulsos a 0.
      Quando o robô começar a andar a contagem será iniciada a partir de 0.
      A contagem de pulsos é colocada a 0 automaticamente quando a contagem alcança 30 000.
  */
  robot.clearEncoderCount();

  //  - - - - - - - - - - - - -

  /*  A função "checkSensors();" verifica os sensores da placa frontal do robô.
      Esta função é um pouco complicada de usar e apenas faz um "digitalRead" a cada pino conectado à
      placa frontal.
      Esta função devolve um byte (8 bits) que deve ser interpretada em binário.
      Cada bit, da direita para a esquerda, significam o seguinte:
      bit 0:  É 1 se o sensor "Near" detetar algo.
      bit 1:  É 1 se o botão CLP for pressionado, isto normalmente acontece quando o robô colide com algo.
      bit 2:  É 1 se o sensor mais à direita detetar uma linha.
      bit 3:  É 1 se o sensor se o sensor da direita detetar uma linha.
      bit 4:  É 1 se o sensor do meio detetar uma linha.
      bit 5:  É 1 se o sensor da esquerda detetar uma linha.
      bit 6:  É 1 se o sensor mais à esquerda detetar uma linha.
  */
  byte info = robot.checkSensors();

  if ( ( info & 0b00000001 ) != 0) { //bit 0
    Serial.println(" Alguma coisa  foi detetada pelo sensor Near. ");
  }
  if ( ( info & 0b00000010 ) != 0) { //bit 1
    Serial.println(" Alguma coisa  foi detetada pelo botão CLP. ");
  }
  if ( ( info & 0b00000100 ) != 0) { //bit 2
    Serial.println(" Uma linha foi detetada pelo sensor mais à dirita. ");
  }
  if ( ( info & 0b00001000 ) != 0) { //bit 3
   Serial.println(" Uma linha foi detetada pelo sensor da direita. ");
  }
  if ( ( info & 0b00010000 ) != 0) { //bit 4
    Serial.println(" Uma linha foi detetada pelo sensor do meio. ");
  }
  if ( ( info & 0b00100000 ) != 0) { //bit 5
    Serial.println(" Uma linha foi detetada pelo sensor da esquerda. ");
  }
  if ( ( info & 0b01000000 ) != 0) { //bit 6
    Serial.println(" Uma linha foi detetada pelo sensor mais à esquerda. ");
  }

  //  - - - - - - - - - - - - -

  /*
   * Para facilitar a leitura infividual de cada pino do módulo de sensores infravermelho
   * foram criadas as seguintes funções.
   * Se o estado do pino for "1" o seu estado é "HIGH" e vice-versa.
   */
   
  bool pinState=0;
  
  pinState = robot.readCLP();

  pinState = robot.readNear();
  
  pinState = robot.readS1();
  
  pinState = robot.readS2();
  
  pinState = robot.readS3();
  
  pinState = robot.readS4();
  
  pinState = robot.readS5();
  
  //  - - - - - - - - - - - - -

  // Para poder usar funções com base em rotações por segundo/minuto e m/s
  // deve primeiro chamar uma vez a função "enSpeedAdj()"

  robot.enSpeedAdj();

  // Para colocar o robô a seguir em frente especificando 
  // a velocidade em rotações por segundo (RPS)
   
  robot.forwardRPS(2.1);

  // Para colocar o robô a recuar especificando 
  // a velocidade em rotações por segundo (RPS)
   
  robot.reverseRPS(1.8);

  // Para colocar o robô a rodar para a direita especificando 
  // a velocidade em rotações por segundo (RPS)
   
  robot.rotateRightRPS(2.3);

  // Para colocar o robô a rodar para a esquerda especificando 
  // a velocidade em rotações por segundo (RPS)
   
  robot.rotateLeftRPS(2.4);
  
  //  - - - - - - - - - - - - -

  // Para colocar o robô a seguir em frente especificando 
  // a velocidade em rotações por minuto (RPM)
   
  robot.forwardRPM(2.1);

  // Para colocar o robô a recuar especificando 
  // a velocidade em rotações por minuto (RPM)
   
  robot.reverseRPM(1.8);

  // Para colocar o robô a rodar para a direita especificando 
  // a velocidade em rotações por minuto (RPM)
   
  robot.rotateRightRPM(2.3);

  // Para colocar o robô a rodar para a esquerda especificando 
  // a velocidade em rotações por minuto (RPM)
   
  robot.rotateLeftRPM(2.4);
  
  //  - - - - - - - - - - - - -

  // Para colocar o robô a seguir em frente especificando 
  // a velocidade em rotações por segundo (RPS)
   
  robot.forwardMS(2.1);

  // Para colocar o robô a recuar especificando 
  // a velocidade em rotações por segundo (RPS)
   
  robot.reverseMS(1.8);

  // Para colocar o robô a rodar para a direita especificando 
  // a velocidade em rotações por segundo (RPS)
   
  robot.rotateRightMS(2.3);

  // Para colocar o robô a rodar para a esquerda especificando 
  // a velocidade em rotações por segundo (RPS)
   
  robot.rotateLeftMS(2.4);
  
  //  - - - - - - - - - - - - -

  // Funções para ler a velocidade da roda direita ou esquerda na unidade especificada:

  float velocidade=0;

  velocidade = robot.getLeftRPS();

  velocidade = robot.getRightRPS();
  
  velocidade = robot.getLeftRPM();

  velocidade = robot.getRightRPM();

  velocidade = robot.getLeftMS();

  velocidade = robot.getRightMS();
}

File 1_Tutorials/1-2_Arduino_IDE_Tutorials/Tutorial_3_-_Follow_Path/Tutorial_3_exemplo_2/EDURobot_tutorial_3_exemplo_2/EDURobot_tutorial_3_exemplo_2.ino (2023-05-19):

#include <iModBot.h>
iModBot robot;

void setup()
 
{
  Serial.begin(115200);
  robot.begin();
}

void loop() 

{
  if ((robot.readS1() == 1) && (robot.readS2() == 1) && (robot.readS3() == 0) && (robot.readS4() == 1) && (robot.readS5() == 1))   
  { 
    robot.forward(110);
    while ((robot.readS1() == 1) && (robot.readS2() == 1) && (robot.readS3() == 0) && (robot.readS4() == 1) && (robot.readS5() == 1))
    {
      ;
    }
  }
  
  else if ((robot.readS1() == 1) && (robot.readS2() == 0) && (robot.readS3() == 1) && (robot.readS4() == 1) && (robot.readS5() == 1))
  {
    robot.rotateLeft(110);
    while ((robot.readS1() == 1) && (robot.readS2() == 0) && (robot.readS3() == 1) && (robot.readS4() == 1) && (robot.readS5() == 1))
    {
      ;
    } 
  }
  
  else if ((robot.readS1() == 0) && (robot.readS2() == 1) && (robot.readS3() == 1) && (robot.readS4() == 1) && (robot.readS5() == 1))
  {
    robot.rotateLeft(110);
    while ((robot.readS1() == 0) && (robot.readS2() == 1) && (robot.readS3() == 1) && (robot.readS4() == 1) && (robot.readS5() == 1))
    {
      ;
    }
  }
  
  else if ((robot.readS1() == 1) && (robot.readS2() == 1) && (robot.readS3() == 1) && (robot.readS4() == 0) && (robot.readS5() == 1))
  {
    robot.rotateRight(110);
    while ((robot.readS1() == 1) && (robot.readS2() == 1) && (robot.readS3() == 1) && (robot.readS4() == 0) && (robot.readS5() == 1))
    {
      ;
    }
  }
  
  else if ((robot.readS1() == 1) && (robot.readS2() == 1) && (robot.readS3() == 1) && (robot.readS4() == 1) && (robot.readS5() == 0))
  {
    robot.rotateRight(110);
    while ((robot.readS1() == 1) && (robot.readS2() == 1) && (robot.readS3() == 1) && (robot.readS4() == 1) && (robot.readS5() == 0))
    {
      ;
    }
  }
  
  else if ((robot.readS1() == 1) && (robot.readS2() == 0) && (robot.readS3() == 0) && (robot.readS4() == 1) && (robot.readS5() == 1))
  {
    robot.rotateLeft(110);
    while ((robot.readS1() == 1) && (robot.readS2() == 0) && (robot.readS3() == 0) && (robot.readS4() == 1) && (robot.readS5() == 1))
    {
      ;
    }
  }
  
  else if ((robot.readS1() == 1) && (robot.readS2() == 1) && (robot.readS3() == 0) && (robot.readS4() == 0) && (robot.readS5() == 1))
  {
    robot.rotateRight(110);
    while ((robot.readS1() == 1) && (robot.readS2() == 1) && (robot.readS3() == 0) && (robot.readS4() == 0) && (robot.readS5() == 1))
    {
      ;
    }
  }
  
  else if ((robot.readS1() == 1) && (robot.readS2() == 1) && (robot.readS3() == 0) && (robot.readS4() == 0) && (robot.readS5() == 0))
  {
    robot.rotateRight(110);
    while ((robot.readS1() == 1) && (robot.readS2() == 1) && (robot.readS3() == 0) && (robot.readS4() == 0) && (robot.readS5() == 0))
    {
      ;
    }
  }

  else if ((robot.readS1() == 0) && (robot.readS2() == 0) && (robot.readS3() == 0) && (robot.readS4() == 1) && (robot.readS5() == 1))
  {
    robot.rotateLeft(110);
    while ((robot.readS1() == 0) && (robot.readS2() == 0) && (robot.readS3() == 0) && (robot.readS4() == 1) && (robot.readS5() == 1))
    {
      ;
    }
  }
  
  else if (((robot.readS1() == 0) && (robot.readS2() == 0) && (robot.readS3() == 0) && (robot.readS4() == 0) && (robot.readS5() == 0)) || (robot.readCLP() == 1) || (robot.distance() <= 10))
  {
      robot.stopMotors();
  }

}
